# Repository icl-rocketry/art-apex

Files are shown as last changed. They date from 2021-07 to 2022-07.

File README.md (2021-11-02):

# art-apex
PCBs and software for ART's APEX rocket

# Contents

1. [Hardware](#Hardware)
2. [Software architecture](#SoftwareArchitecture)
3. [Next Steps](#NextSteps)

## Hardware

The flight computer for Apex consists of the following components:

1. [Tiny2040](https://shop.pimoroni.com/products/tiny-2040) microcontroller - for controlling each of the components
2. [BNO085](https://learn.adafruit.com/adafruit-9-dof-orientation-imu-fusion-breakout-bno085) 9DoF IMU - for recording and fusing flight data
3. [DPS310](https://www.infineon.com/cms/en/product/sensor/pressure-sensors/pressure-sensors-for-iot/dps310/) barometer - for recording altitude information
4. [Sim800L](https://nettigo.eu/products/sim800l-gsm-grps-module) GPRS/GSM module - for communication between the flight computer and ground team
5. [Adafruit mini GPS PA1010D](https://www.adafruit.com/product/4415) GPS module - for recovery
6. 3.7V 200maH LiPo battery - for powering the system
7. A 104 decibel speaker - for recovery

The Tiny2040 is connected to the BNO085, DPS310 and PA1010D via an I2C connection using GPIO pins 26 and 27. The Tiny2040 is connected to the Sim800L module via a UART connection using GPIO pins 4 and 5.

The SIM8000L **must** be isolated when the Tiny2040 is connected to USB, or else it will be fried.

## Software

The filesystem on board the Tiny2040 will look like this:
```
📦src
 ┣ 📂lib
 ┃ ┣ 📂adafruit_bno08x
 ┃ ┃ ┣ 📜debug.py
 ┃ ┃ ┣ 📜i2c.py
 ┃ ┃ ┗ 📜__init__.py
 ┃ ┣ 📂adafruit_bus_device
 ┃ ┃ ┣ 📜i2c_device.mpy
 ┃ ┃ ┣ 📜spi_device.mpy
 ┃ ┃ ┗ 📜__init__.py
 ┃ ┣ 📂adafruit_register
 ┃ ┃ ┣ 📜i2c_bcd_alarm.mpy
 ┃ ┃ ┣ 📜i2c_bcd_datetime.mpy
 ┃ ┃ ┣ 📜i2c_bit.mpy
 ┃ ┃ ┣ 📜i2c_bits.mpy
 ┃ ┃ ┣ 📜i2c_struct.mpy
 ┃ ┃ ┣ 📜i2c_struct_array.mpy
 ┃ ┃ ┗ 📜__init__.py
 ┃ ┣ 📜adafruit_dps310.mpy
 ┃ ┗ 📜adafruit_gps.py
 ┣ 📜boot.py
 ┣ 📜code.py
 ┣ 📜gps.py
 ┣ 📜led.py
 ┣ 📜phone.number
 ┣ 📜sensors.py
 ┣ 📜sms.py
 ┣ 📜speaker.py
 ┗ 📜state_machine.py
```

All folders inside the lib directory are libraries required for the Tiny2040 to interact with components. None of these files should be changed, except for lib/adafruit_bno08x/\_\_init__.py, where `_DEFAULT_REPORT_INTERVAL` should be set to 35ms. **Pro tip: don't lower this if you want to launch**.

`boot.py` runs right after the Tiny2040 boots up. Its sole purpose is to grant write permission to the Tiny2040. Due to the implementation of CircuitPython's filesystem either a laptop or the Tiny2040, can write to the Tiny2040's filesystem, so this ensures that the Tiny2040 has this permission.

`code.py` runs the main code of the AAS. It essentially runs through the state machine defined in `state_machine.py`.

`gps.py`, `led.py`, `sensors.py`, `speaker.py` and `sms.py` are [adapters](https://www.tutorialspoint.com/design_pattern/adapter_pattern.htm) around the peripherals discussed above. The adapter pattern is used to decouple the rest of the code from the specifics of these devices.

`state_machine.py` contains the bulk of the flight logic. It describes a (linear) [finite state machine](https://en.wikipedia.org/wiki/Finite-state_machine) with 5 states.

1. Diagnostic - initialises sensors and sends initial messages
2. Calibration - calibrates the BNO085 as described [here](https://www.ceva-dsp.com/wp-content/uploads/2019/10/BNO080_085-Datasheet.pdf) on page 39
3. Preflight - sleeps until the launch command is sent.
4. Flight - records 5 minutes of flight data, and sends data to the telemetry service.
5. Postflight - sends the rocket's location/plays the siren when asked. Also plays the siren once every 30 seconds.

The Flight stage is the most involved, so a brief explanation of its code can be found below.

```py
def run(self):
    i = 0
    led.colour(255, 0, 0)

    #Problem:
    #Sim module will need long (50ms+) waits to work
    #But we can't afford that in a single threaded environment
    #Solution:
    #Use pkt_wait to provide the sleeps
    pkt_wait = 1
    pkt = bytearray(sensors.data_size * 4)
    self._sms.connect()

    while i < self._flight_time:
        pkt_wait -= 1
        i += 1
        start = millis()
        data = self._sensors.get()
        for reading in data:
            self._sensor_storage.write(struct.pack("f", reading))

        if pkt_wait == 0:
            pkt[0:4] = struct.pack("f", data[0]) #time
            for j in range(4):
                pkt[4*j:4*(j+1)] = struct.pack("f", data[j+4])
            
            pkt[20:24] = struct.pack("f", data[10]) #altitude
            pkt_wait = self._sms.send_pkt(pkt)
        end = millis()
        sleep_ms(max(0, self._delay - (end - start)))

    self._sensor_storage.flush()
    self._sensor_storage.close()
    self._sms.disconnect()
    return postflight(self._sms, self._gps)
```

```py
led.colour(255, 0, 0)
```
First the Tiny2040's led is set to red to indicate flight.

```py
pkt_wait = 1
pkt = bytearray(sensors.data_size * 4)
self._sms.connect()
```
This code relates to the telemetry service. The Sim800L will connect to GPRS here (the internet) and send appropriate data via UDP. To save space, it will group several readings into a single packet.

```py
while i < self._flight_time:
    pkt_wait -= 1
    i += 1
    start = millis()
    data = self._sensors.get()
    for reading in data:
        self._sensor_storage.write(struct.pack("f", reading))

    if pkt_wait == 0:
        pkt[0:4] = struct.pack("f", data[0]) #time
        for j in range(4):
            pkt[4*j:4*(j+1)] = struct.pack("f", data[j+4])
        
        pkt[20:24] = struct.pack("f", data[10]) #altitude
        pkt_wait = self._sms.send_pkt(pkt)
    end = millis()
    sleep_ms(max(0, self._delay - (end - start)))
```

This is the main flight loop. It waits for `self._flight_time` readings to occur (assuming each reading takes at most `self._delay` ms).

```py
start = millis()
data = self._sensors.get()
for reading in data:
    self._sensor_storage.write(struct.pack("f", reading))
```
This code takes sensor readings, and records the time that they were taken, then writes them into a file. The values are stored as 32bit floating point numbers, to save space.
Note: the time recorded is milliseconds from the start.

```py
if pkt_wait == 0:
    pkt[0:4] = struct.pack("f", data[0]) #time
    for j in range(4):
        pkt[4*j:4*(j+1)] = struct.pack("f", data[j+4])
    
    pkt[20:24] = struct.pack("f", data[10]) #altitude
    pkt_wait = self._sms.send_pkt(pkt)
```
This adds the readings into the packet defined earlier, and if the packet is full it sends them.

The `pkt_wait` variable is used to solve a problem, which is that the Sim800l needs to wait around 200ms after it's sent a packet, before being able to send another one. However we can't perform this wait in the main loop, as that would lead to large delays in between recordings, so we define the `pkt_wait` variable to indicate whether we can send a packet. This allows us to use the main loop as a pseudo sleep (at the time of writing, the `uasynchio` library was not available).

```py
end = millis()
sleep_ms(max(0, self._delay - (end - start)))
```
This ensures that we always sleep for at least 50ms, regardless of how long different components take to work.

```py
self._sensor_storage.flush()
self._sensor_storage.close()
self._sms.disconnect()
return postflight(self._sms, self._gps)
```
Finally we flush the recordings, and close the file, then disconnect the Sim800L from GPRS and move on to the postflight stage. 

The end.

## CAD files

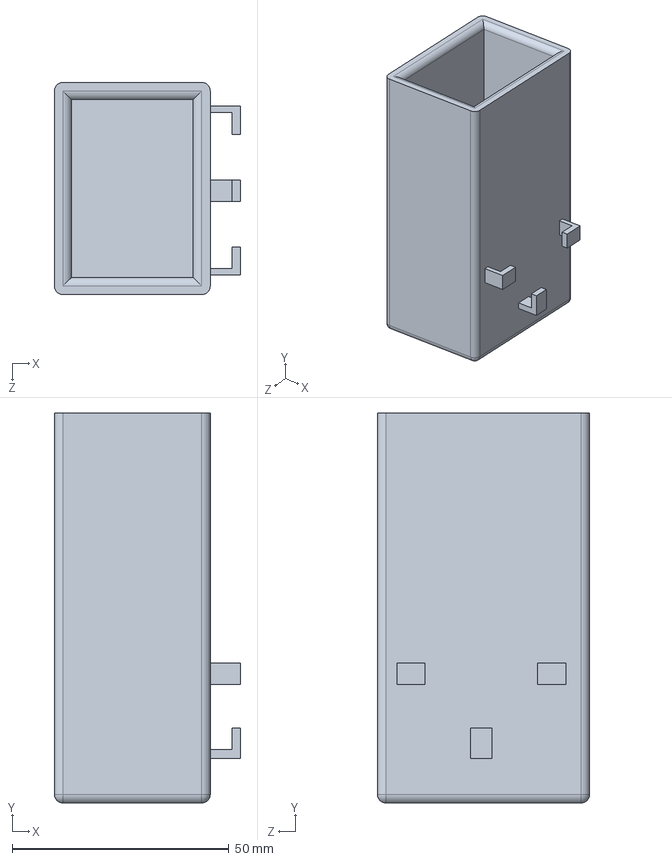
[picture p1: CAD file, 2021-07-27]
apex/test_bay/main.SLDPRT
43.0 x 90.0 x 49.0 mm

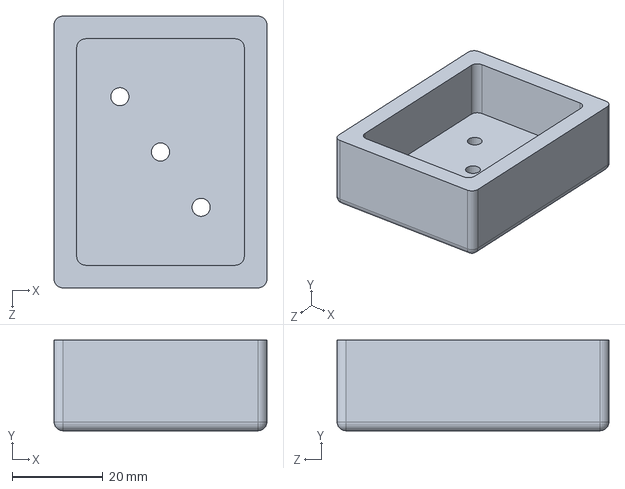
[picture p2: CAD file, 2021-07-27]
apex/test_bay/lid.SLDPRT
47.0 x 20.0 x 60.0 mm

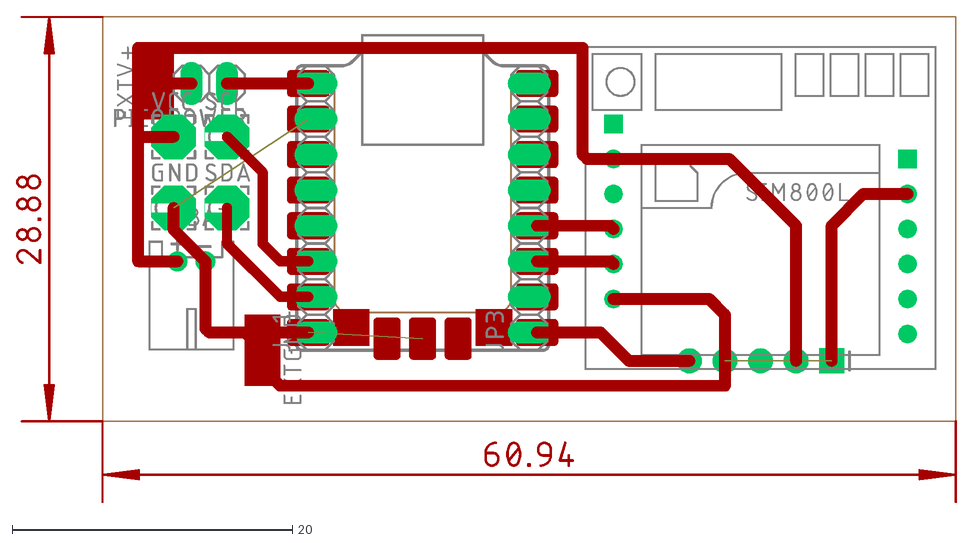
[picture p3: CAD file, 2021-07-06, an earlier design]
PCB/APEX/v2/lower_traced.dxf
67.2 x 34.8

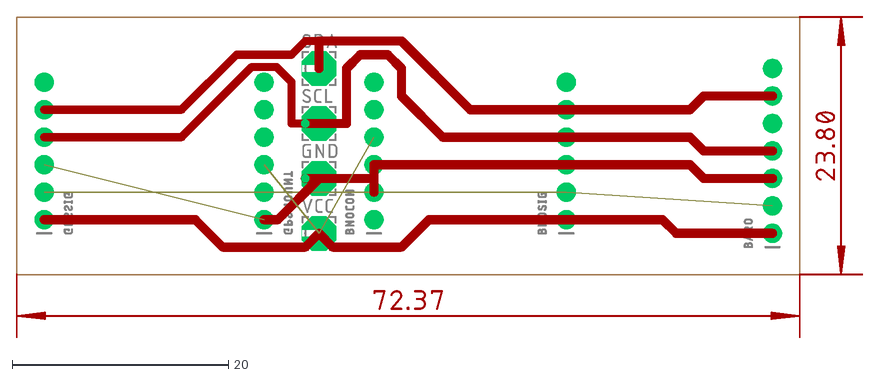
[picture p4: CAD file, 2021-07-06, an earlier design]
PCB/APEX/v2/upper_traced.dxf
78.3 x 29.7

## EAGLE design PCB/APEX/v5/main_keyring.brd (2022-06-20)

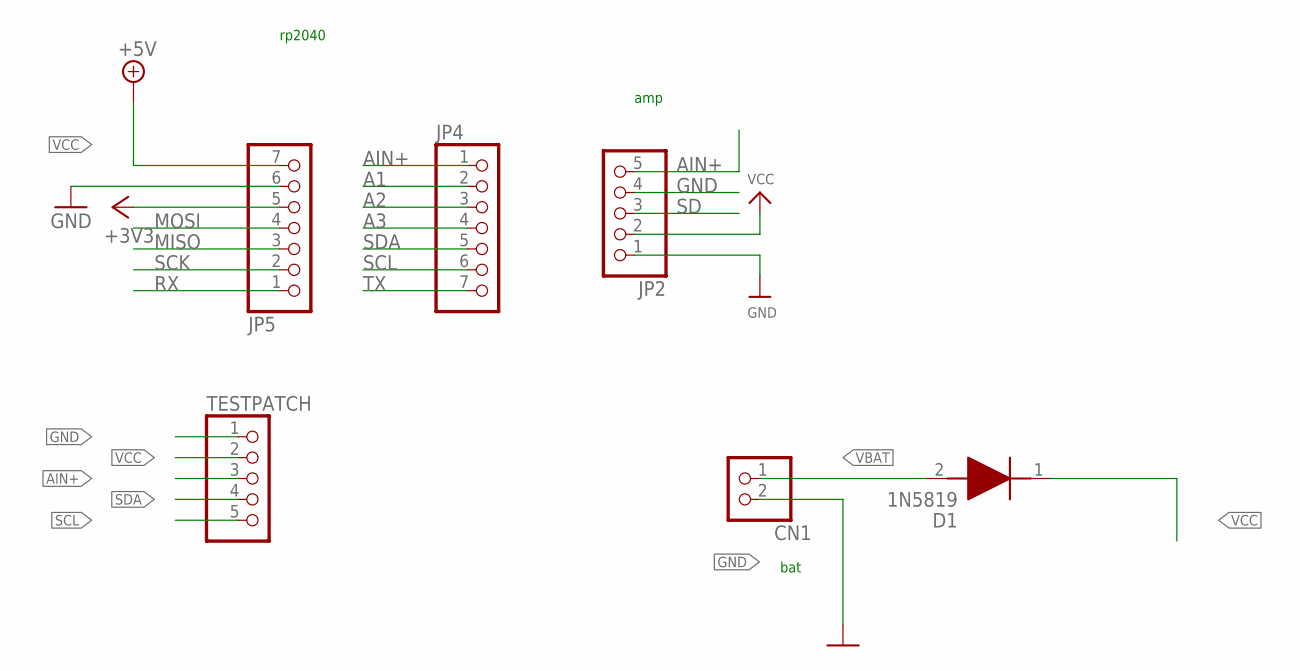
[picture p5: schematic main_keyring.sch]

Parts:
CN1: JST_2PIN-THM; JST-PH-2-THM
D1: 1N5819; DIOAD1414W86L464D238
JP2: HEADER-1X570MIL; 1X05_ROUND_70
JP4, JP5: HEADER-1X7; 1X07_OVAL
TESTPATCH: PINHD-1X5; 1X05

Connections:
+3V3: JP5.5
A1: JP4.2
A2: JP4.3
A3: JP4.4
AIN+: JP2.5, JP4.1, TESTPATCH.3
GND: CN1.2 (1), JP2.1, JP2.4, JP5.6, TESTPATCH.1
MISO: JP5.3
MOSI: JP5.4
RX: JP5.1
SCK: JP5.2
SCL: JP4.6, TESTPATCH.5
SD: JP2.3
SDA: JP4.5, TESTPATCH.4
TX: JP4.7
VBAT: CN1.1 (2), D1.2 (A)
VCC: D1.1 (K), JP2.2, JP5.7, TESTPATCH.2

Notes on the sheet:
amp
bat
rp2040

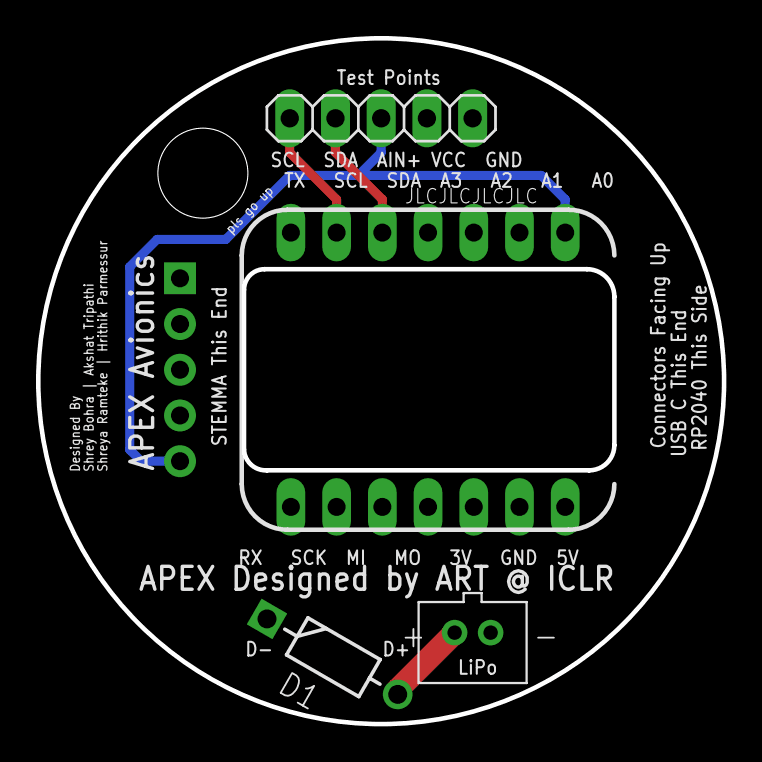
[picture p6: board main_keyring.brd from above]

Board: 2 copper layers, 38.1 x 38.1 mm, 6 parts (1 on the bottom side), 6 nets.

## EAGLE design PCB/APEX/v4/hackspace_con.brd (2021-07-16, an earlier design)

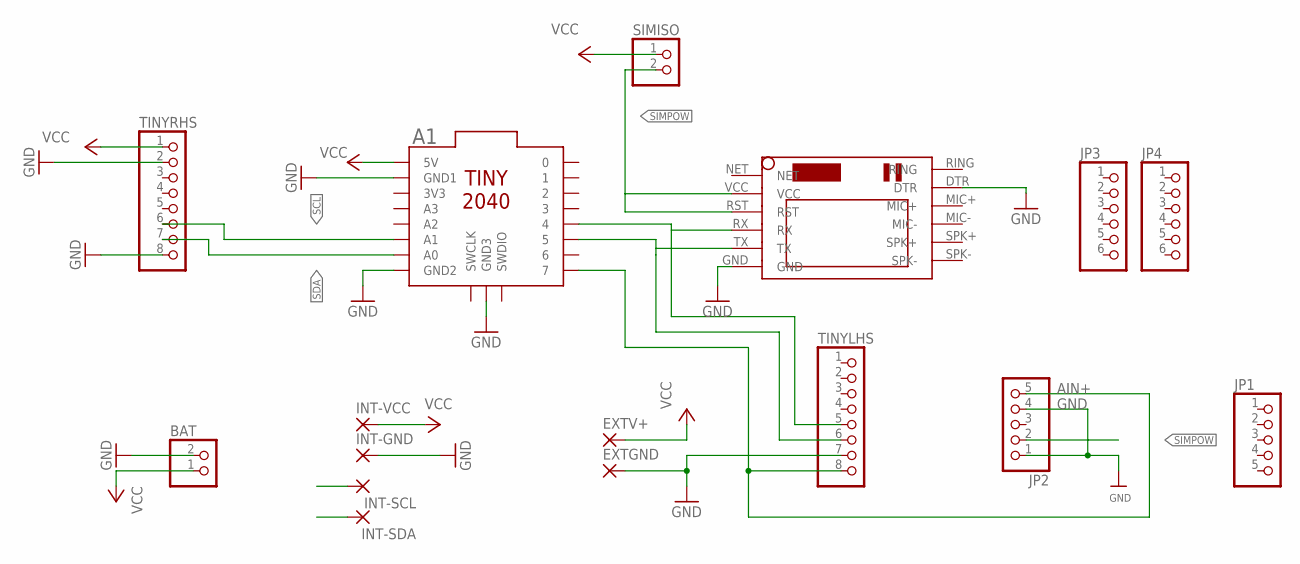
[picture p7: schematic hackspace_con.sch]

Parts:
A1: TINY2040
BAT: JST_2PIN-THM-RA; JST-PH-2-THM-RA
EXTGND: SMD5; SMD2,54-5,08
EXTV+: SMD5; SMD2,54-5,08
INT-GND: 3,17/1,1
INT-SCL: 3,17/1,1
INT-SDA: 3,17/1,1
INT-VCC: 3,17/1,1
JP1: PINHD-1X5; 1X05
JP2: HEADER-1X570MIL; 1X05_ROUND_70
JP3, JP4: PINHD-1X6; 1X06
SIMISO: PINHD-1X2; 1X02
TINYLHS: PINHD-1X8; 1X08
TINYRHS: PINHD-1X8; 1X08
U$1: SIM800LMODULE

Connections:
AIN+: A1.7, JP2.5, TINYLHS.8
GND: A1.GND1, A1.GND2, A1.GND3, BAT.2 (1), EXTGND.1, INT-GND.1, JP2.1, JP2.4, TINYLHS.7, TINYRHS.2, TINYRHS.8, U$1.DTR, U$1.GND
RX: A1.4, TINYLHS.5, U$1.RX
SCL: A1.A1, INT-SCL.1, TINYRHS.6
SDA: A1.A0, INT-SDA.1, TINYRHS.7
SIMPOW: JP2.2, SIMISO.2, U$1.RST, U$1.VCC
TX: A1.5, TINYLHS.6, U$1.TX
VCC: A1.5V, BAT.1 (2), EXTV+.1, INT-VCC.1, SIMISO.1, TINYRHS.1

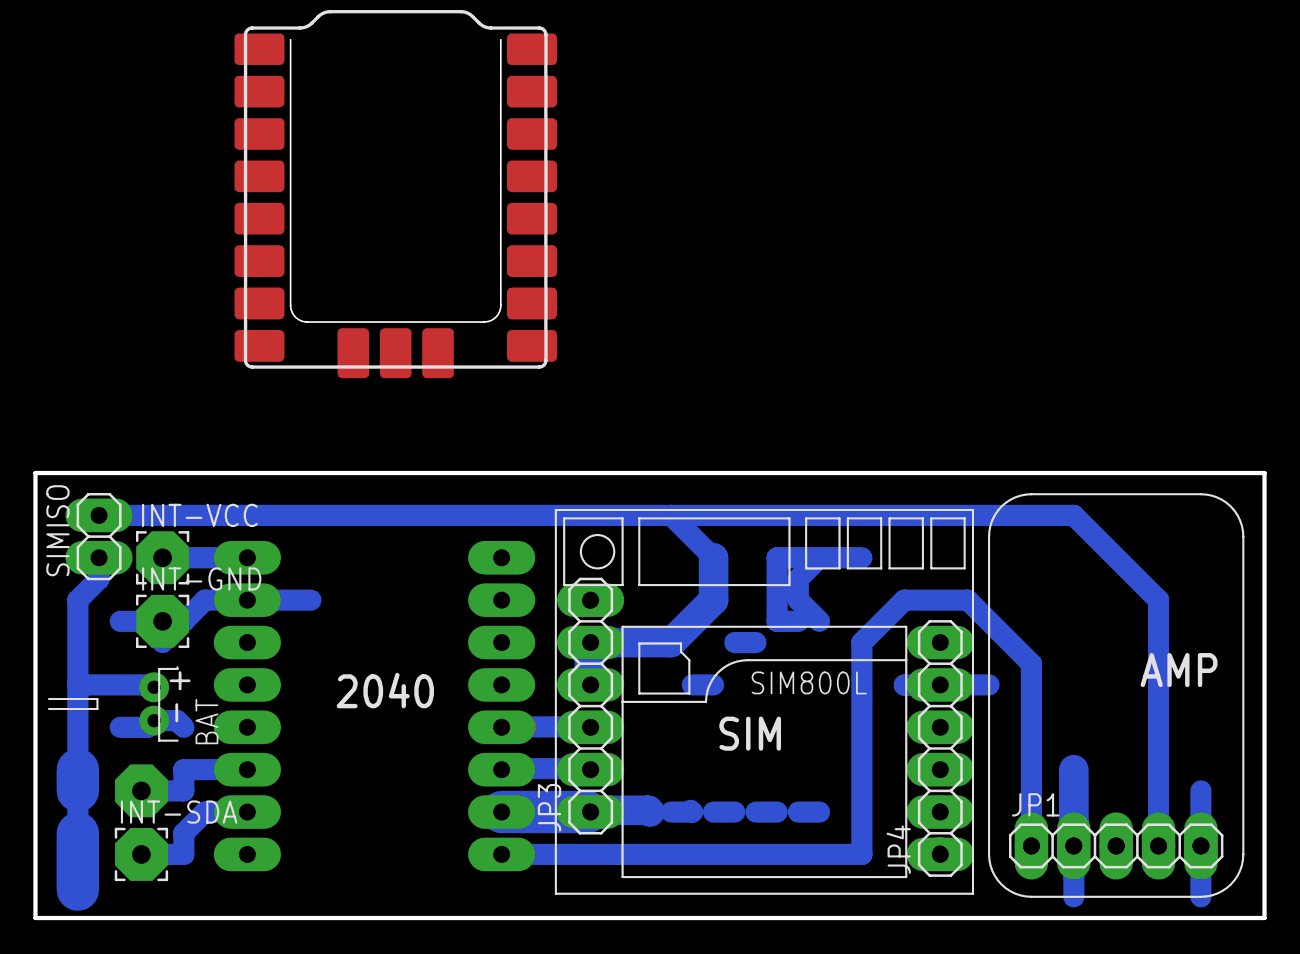
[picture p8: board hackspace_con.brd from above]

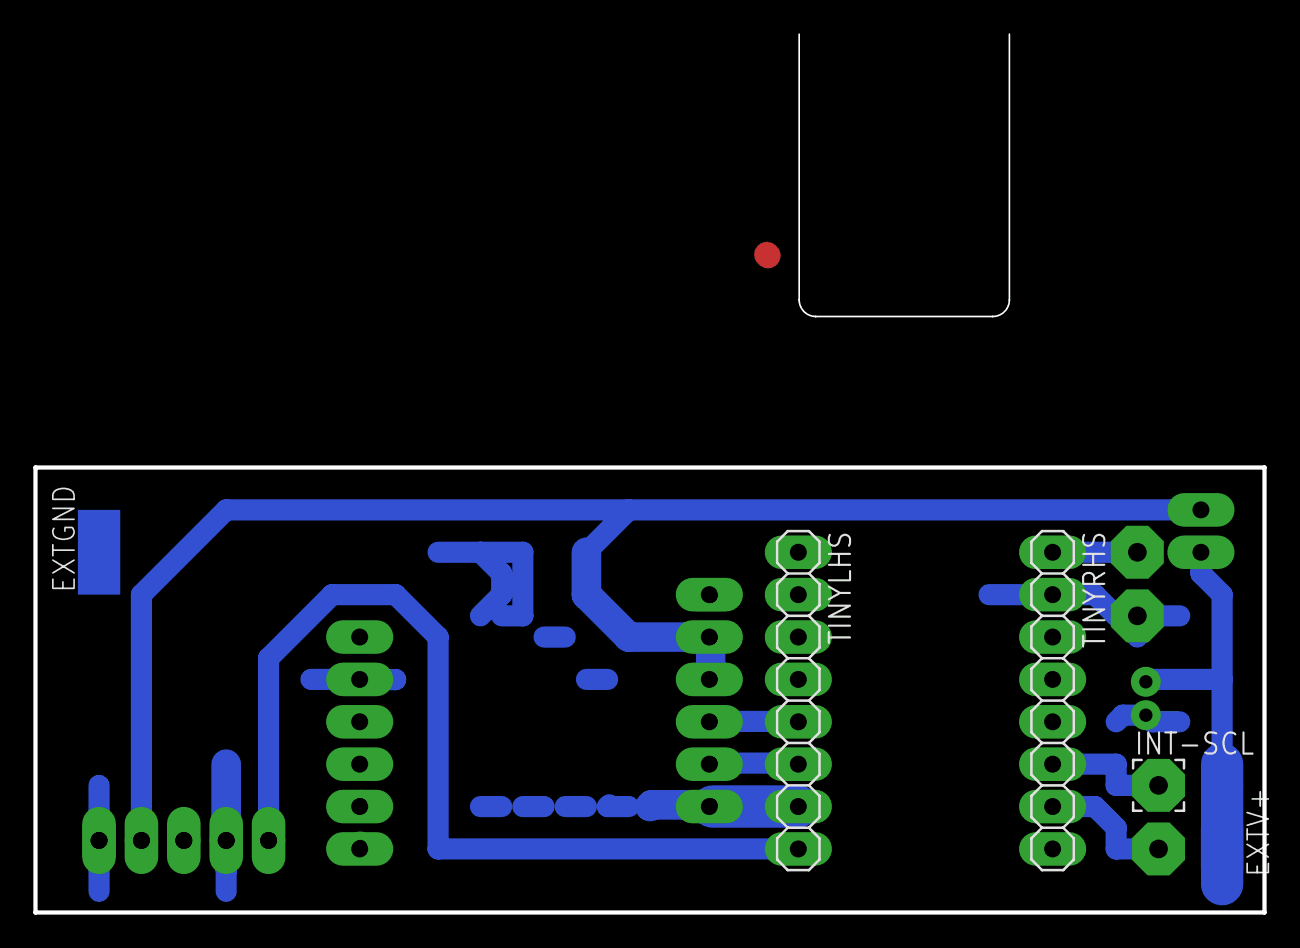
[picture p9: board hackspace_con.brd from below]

Board: 2 copper layers, 73.7 x 26.7 mm, 16 parts (5 on the bottom side), 8 nets.

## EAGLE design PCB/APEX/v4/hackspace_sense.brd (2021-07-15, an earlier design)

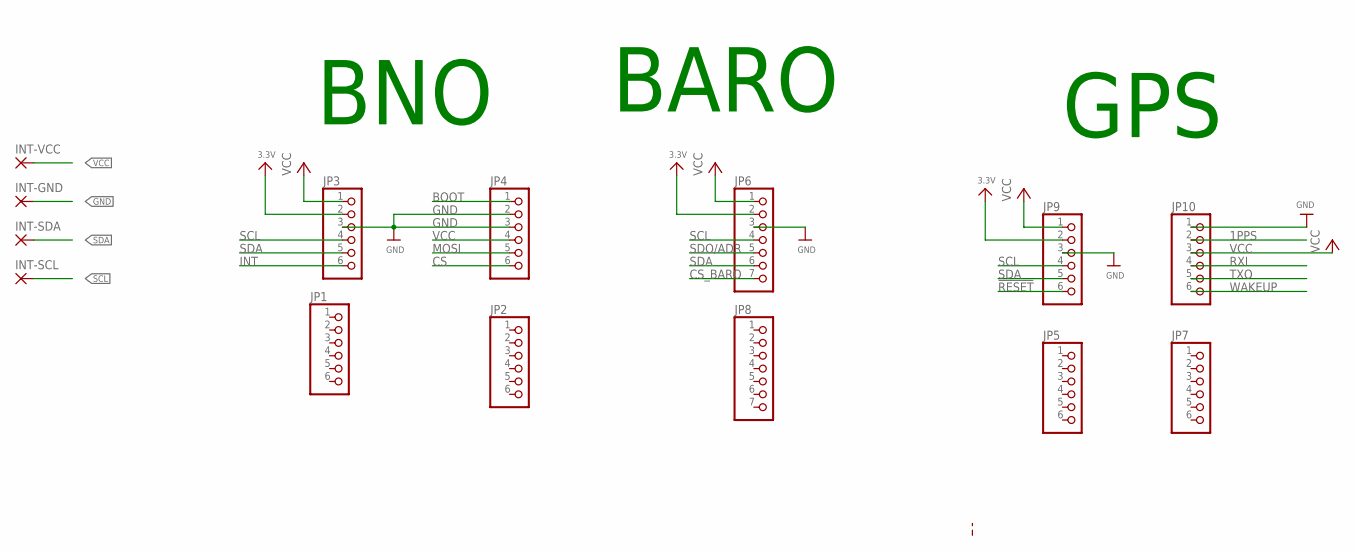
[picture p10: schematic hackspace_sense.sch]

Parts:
INT-GND: 3,17/1,1
INT-SCL: 3,17/1,1
INT-SDA: 3,17/1,1
INT-VCC: 3,17/1,1
JP1, JP2, JP5, JP7: PINHD-1X6; 1X06
JP3, JP4, JP9, JP10: HEADER-1X670MIL; 1X06_ROUND_70
JP6: HEADER-1X770MIL; 1X07_ROUND_70
JP8: PINHD-1X7; 1X07

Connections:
1PPS: JP10.2
3.3V_BARO: JP6.2
3.3V_BNO: JP3.2
3.3V_GPS: JP9.2
!RESET: JP9.6
BOOT: JP4.1
CS: JP4.6
CS_BARO: JP6.7
GND: INT-GND.1, JP3.3, JP4.2, JP4.3, JP6.3, JP9.3, JP10.1
INT: JP3.6
MOSI: JP4.5
RXI: JP10.4
SCL: INT-SCL.1, JP3.4, JP6.4, JP9.4
SDA: INT-SDA.1, JP3.5, JP6.6, JP9.5
SDO/ADR: JP6.5
TXO: JP10.5
VCC: INT-VCC.1, JP3.1, JP4.4, JP6.1, JP9.1, JP10.3
WAKEUP: JP10.6

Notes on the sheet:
BNO
BARO
GPS

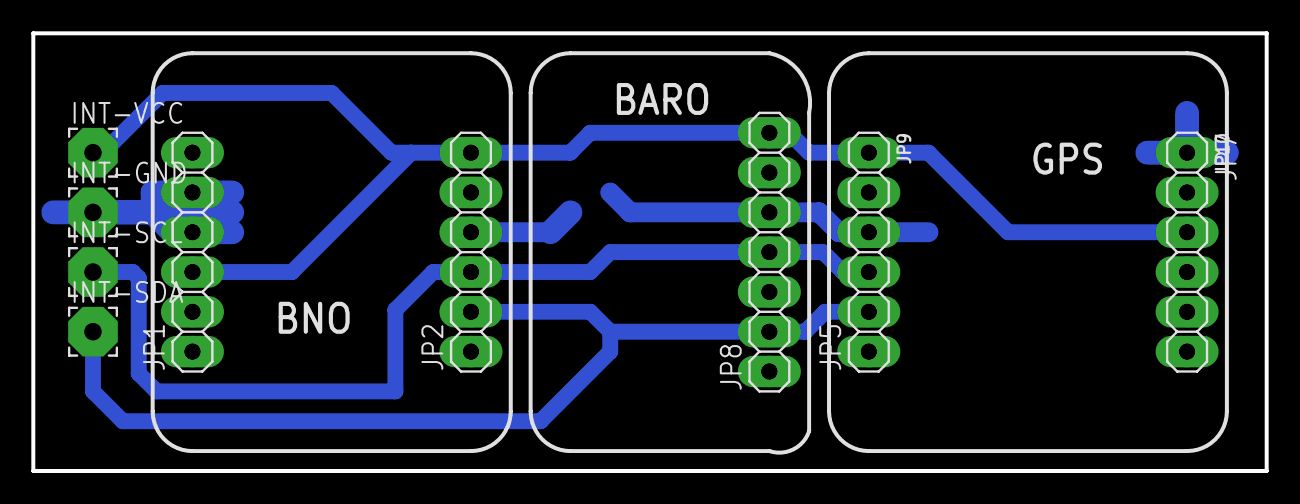
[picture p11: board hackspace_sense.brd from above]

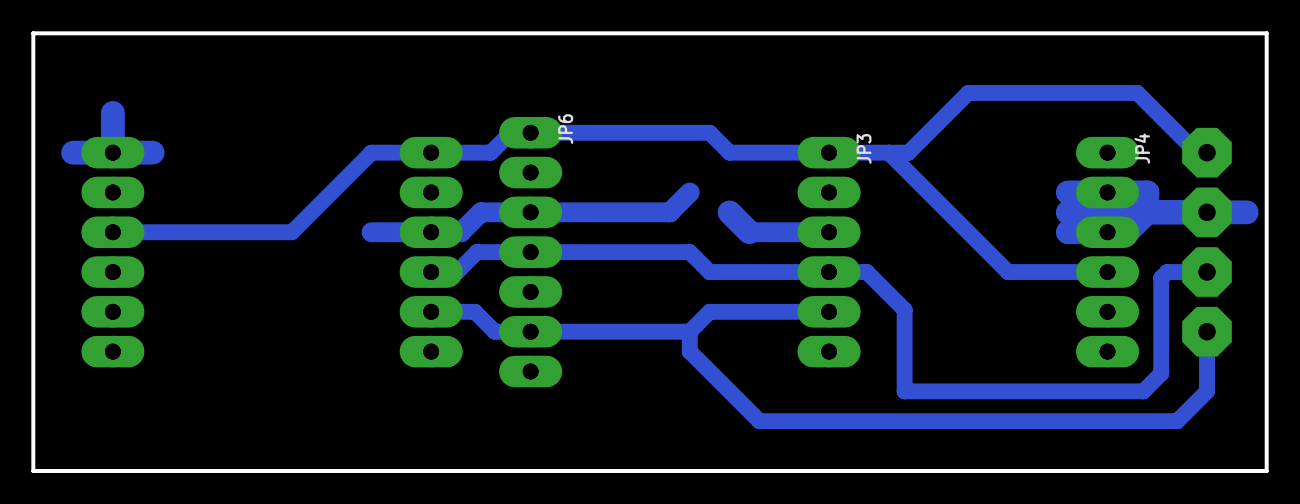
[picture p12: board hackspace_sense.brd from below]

Board: 2 copper layers, 78.7 x 27.9 mm, 14 parts (3 on the bottom side), 4 nets.

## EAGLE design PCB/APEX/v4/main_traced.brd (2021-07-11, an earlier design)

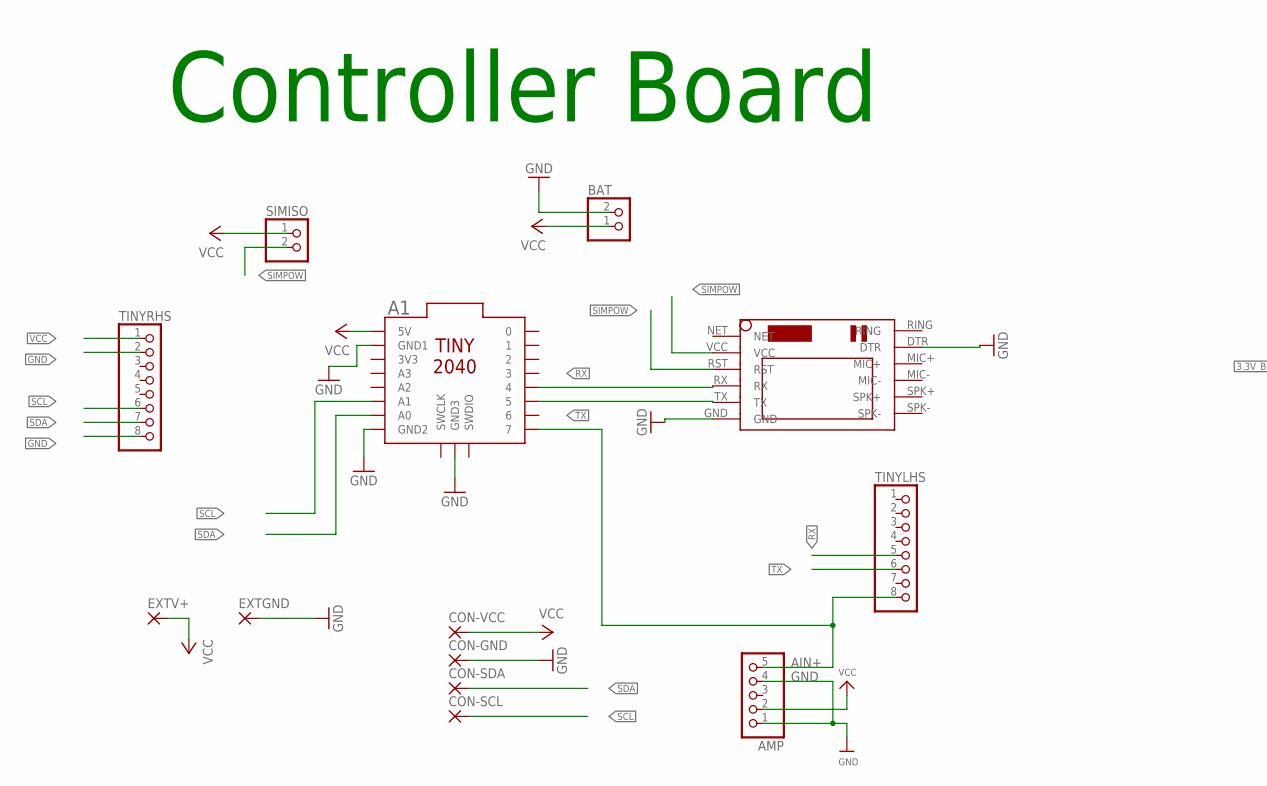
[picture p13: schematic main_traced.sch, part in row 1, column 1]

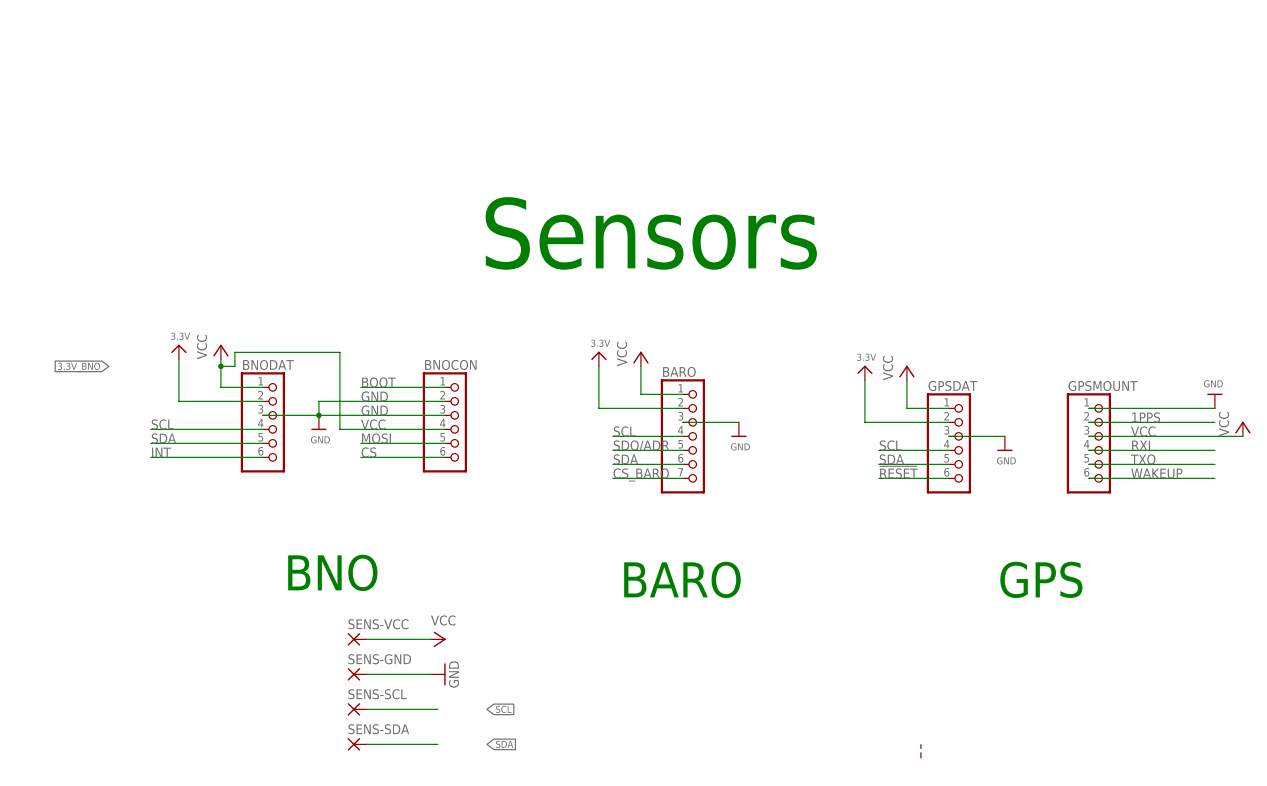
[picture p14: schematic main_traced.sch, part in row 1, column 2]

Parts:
A1: TINY2040
AMP: HEADER-1X570MIL; 1X05_ROUND_70
BARO: HEADER-1X770MIL; 1X07_ROUND_70
BAT: JST_2PIN-THM-RA; JST-PH-2-THM-RA
BNOCON: HEADER-1X670MIL; 1X06_ROUND_70
BNODAT: HEADER-1X670MIL; 1X06_ROUND_70
CON-GND: 3,17/1,3
CON-SCL: 3,17/1,3
CON-SDA: 3,17/1,3
CON-VCC: 3,17/1,3
EXTGND: SMD5; SMD2,54-5,08
EXTV+: SMD5; SMD2,54-5,08
GPSDAT: HEADER-1X670MIL; 1X06_ROUND_70
GPSMOUNT: HEADER-1X670MIL; 1X06_ROUND_70
SENS-GND: 3,17/1,3
SENS-SCL: 3,17/1,3
SENS-SDA: 3,17/1,3
SENS-VCC: 3,17/1,3
SIMISO: PINHD-1X2; 1X02
TINYLHS: PINHD-1X8; 1X08
TINYRHS: PINHD-1X8; 1X08
U$1: SIM800LMODULE

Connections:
1PPS: GPSMOUNT.2
3.3V_2: BARO.2
3.3V_3: GPSDAT.2
3.3V_BNO: BNODAT.2
!RESET: GPSDAT.6
AIN+: A1.7, AMP.5, TINYLHS.8
BOOT: BNOCON.1
CS: BNOCON.6
CS_BARO: BARO.7
GND: A1.GND1, A1.GND2, A1.GND3, AMP.1, AMP.4, BARO.3, BAT.2 (1), BNOCON.2, BNOCON.3, BNODAT.3, CON-GND.1, EXTGND.1, GPSDAT.3, GPSMOUNT.1, SENS-GND.1, TINYRHS.2, TINYRHS.8, U$1.DTR, U$1.GND
INT: BNODAT.6
MOSI: BNOCON.5
RX: A1.4, TINYLHS.5, U$1.RX
RXI: GPSMOUNT.4
SCL: A1.A1, BARO.4, BNODAT.4, CON-SCL.1, GPSDAT.4, SENS-SCL.1, TINYRHS.6
SDA: A1.A0, BARO.6, BNODAT.5, CON-SDA.1, GPSDAT.5, SENS-SDA.1, TINYRHS.7
SDO/ADR: BARO.5
SIMPOW: SIMISO.2, U$1.RST, U$1.VCC
TX: A1.5, TINYLHS.6, U$1.TX
TXO: GPSMOUNT.5
VCC: A1.5V, AMP.2, BARO.1, BAT.1 (2), BNOCON.4, BNODAT.1, CON-VCC.1, EXTV+.1, GPSDAT.1, GPSMOUNT.3, SENS-VCC.1, SIMISO.1, TINYRHS.1
WAKEUP: GPSMOUNT.6

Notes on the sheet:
Controller Board
BNO
BARO
GPS
Sensors

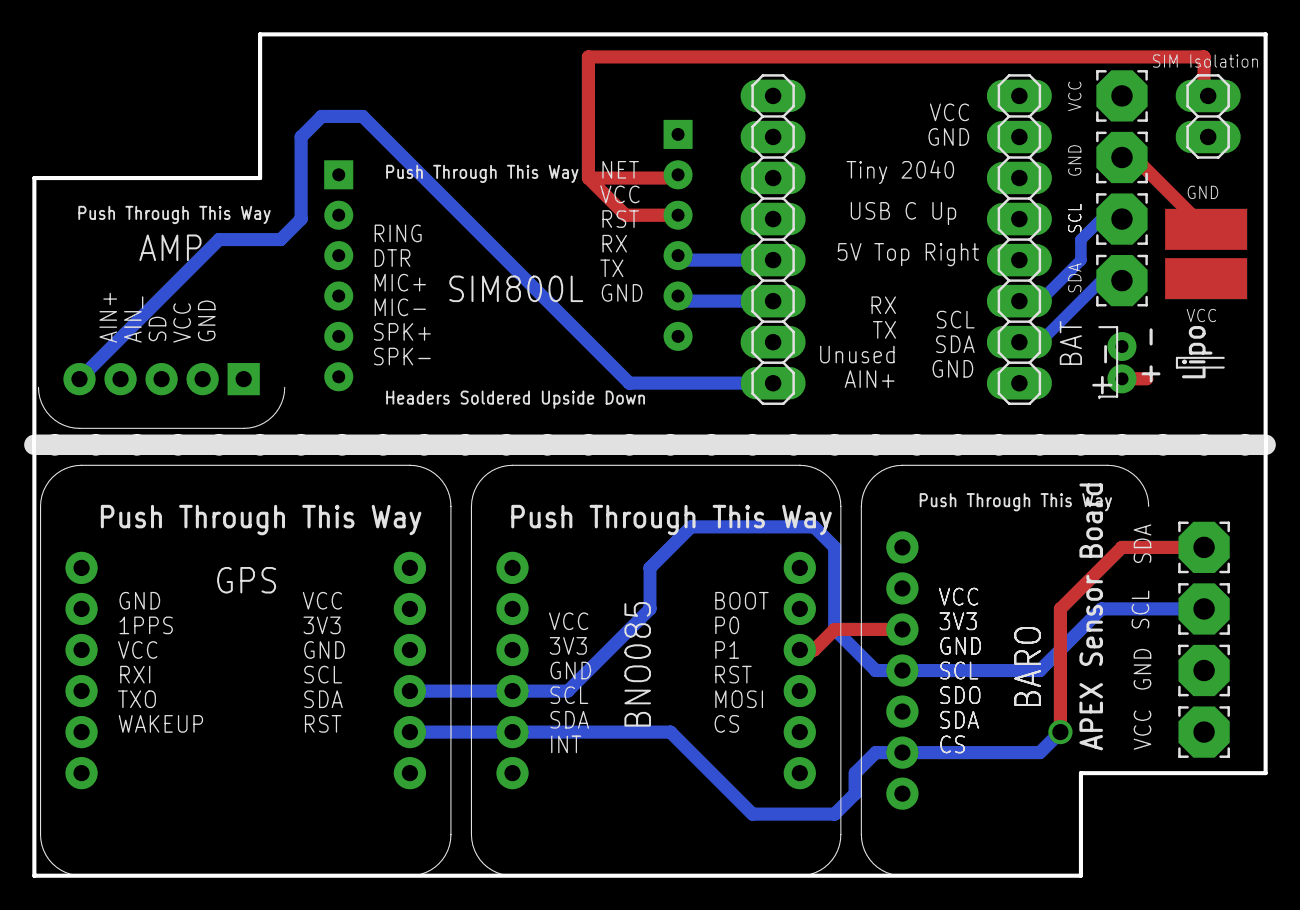
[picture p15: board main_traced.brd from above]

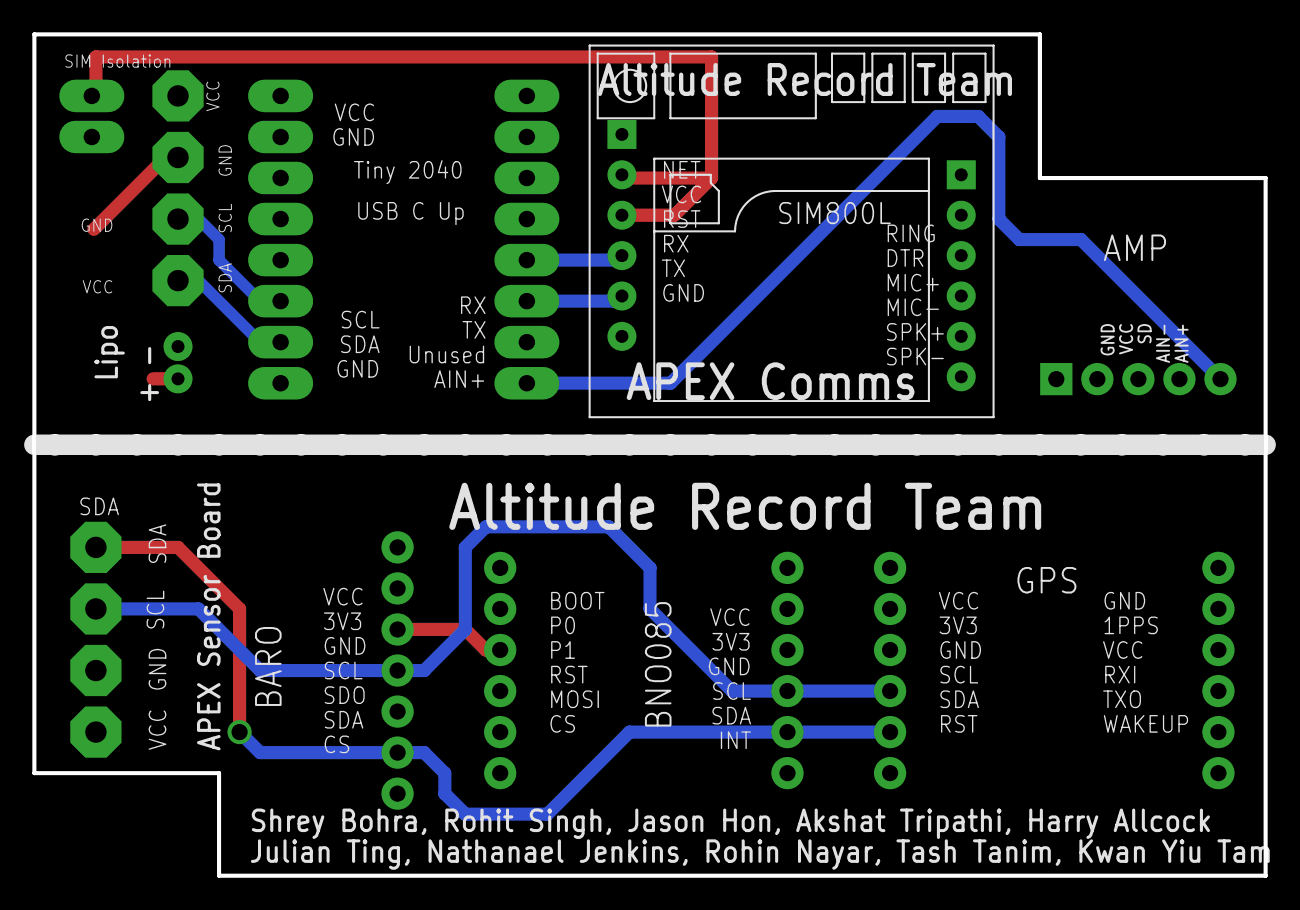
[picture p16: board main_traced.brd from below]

Board: 2 copper layers, 76.2 x 52.1 mm, 21 parts (3 on the bottom side), 8 nets.

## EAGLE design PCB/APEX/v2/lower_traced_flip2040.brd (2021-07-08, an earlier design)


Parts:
A1: TINY2040
BAT: JST_2PIN-THM-RA; JST-PH-2-THM-RA
GND: 3,17/1,1
JP2: HEADER-1X570MIL; 1X05_ROUND_70
PICOPOWER: PINHD-1X2; 1X02
SCL: 3,17/1,1
SDA: 3,17/1,1
TINYLHS: PINHD-1X8; 1X08
TINYRHS: PINHD-1X8; 1X08
U$2: SIM800LMODULE
VCC: 3,17/1,1

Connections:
AIN+: A1.7, JP2.5, TINYLHS.8
GND: A1.GND1, A1.GND2, A1.GND3, BAT.2 (1), GND.1, JP2.1, JP2.4, TINYRHS.2, TINYRHS.8, U$2.DTR, U$2.GND
unnamed: A1.4, TINYLHS.5, U$2.RX
unnamed: A1.5, TINYLHS.6, U$2.TX
unnamed: A1.A1, SCL.1, TINYRHS.6
unnamed: A1.A0, SDA.1, TINYRHS.7
unnamed: A1.5V, PICOPOWER.1, TINYRHS.1
unnamed: A1.6, TINYLHS.7
unnamed: A1.3, TINYLHS.4
unnamed: A1.2, TINYLHS.3
unnamed: A1.1, TINYLHS.2
unnamed: A1.0, TINYLHS.1
unnamed: A1.A2, TINYRHS.5
unnamed: A1.A3, TINYRHS.4
unnamed: A1.3V3, TINYRHS.3
VCC: BAT.1 (2), JP2.2, PICOPOWER.2, U$2.VCC, VCC.1



Board: 2 copper layers, 60.9 x 28.9 mm, 11 parts (3 on the bottom side), 16 nets.

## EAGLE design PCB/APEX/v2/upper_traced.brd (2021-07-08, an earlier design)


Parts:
BARO: HEADER-1X770MIL; 1X07_ROUND_70
BNOCON: HEADER-1X670MIL; 1X06_ROUND_70
BNOSIG: HEADER-1X670MIL; 1X06_ROUND_70
GND: 3,17/1,1
GPSMOUNT: HEADER-1X670MIL; 1X06_ROUND_70
GPSSIG: HEADER-1X670MIL; 1X06_ROUND_70
SCL: 3,17/1,1
SDA: 3,17/1,1
VCC: 3,17/1,1

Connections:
+3V3: BARO.2, BNOSIG.2, GPSSIG.2
GND: BARO.3, BNOCON.2, BNOCON.3, BNOSIG.3, GND.1, GPSMOUNT.1, GPSSIG.3
SCL: BARO.4, BNOSIG.4, GPSSIG.4, SCL.1
SDA: BARO.6, BNOSIG.5, GPSSIG.5, SDA.1
VCC: BARO.1, BNOCON.4, BNOSIG.1, GPSMOUNT.3, GPSSIG.1, VCC.1

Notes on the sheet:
bno
dps
gps



Board: 2 copper layers, 72.4 x 23.8 mm, 9 parts (2 on the bottom side), 5 nets.

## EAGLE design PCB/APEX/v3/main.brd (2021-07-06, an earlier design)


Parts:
AMP: HEADER-1X570MIL; 1X05_ROUND_70
BARO: HEADER-1X770MIL; 1X07_ROUND_70
BNOCON: HEADER-1X670MIL; 1X06_ROUND_70
BNOSIG: HEADER-1X670MIL; 1X06_ROUND_70
CN1: JST_2PIN-THM-RA; JST-PH-2-THM-RA
EXTGND: SMD5; SMD2,54-5,08
EXTV+: SMD5; SMD2,54-5,08
GPSMOUNT: HEADER-1X670MIL; 1X06_ROUND_70
GPSSIG: HEADER-1X670MIL; 1X06_ROUND_70
RP2040: TINY2040
RPSWITCH: PINHD-1X2; 1X02
U$1: SIM800LMODULE

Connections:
3.3V: BARO.2, BNOSIG.2, GPSSIG.2
AIN+: AMP.5, RP2040.7
GND: AMP.1, AMP.4, BARO.3, BNOCON.2, BNOCON.3, BNOSIG.3, CN1.2 (1), EXTGND.1, GPSSIG.3, RP2040.GND1, RP2040.GND2, RP2040.GND3, U$1.DTR, U$1.GND
unnamed: RP2040.4, U$1.RX
unnamed: RP2040.5, U$1.TX
unnamed: RP2040.5V, RPSWITCH.1
SCL: BARO.4, BNOSIG.4, GPSSIG.4, RP2040.A1
SDA: BARO.6, BNOSIG.5, GPSSIG.5, RP2040.A0
VCC: AMP.2, BARO.1, BNOCON.4, BNOSIG.1, CN1.1 (2), EXTV+.1, GPSSIG.1, RPSWITCH.2, U$1.VCC

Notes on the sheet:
bno
dps
gps
amp


Board: 2 copper layers, 160.0 x 100.0 mm, 12 parts (0 on the bottom side), 9 nets.

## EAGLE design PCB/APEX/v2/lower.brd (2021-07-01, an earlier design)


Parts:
A1: TINY2040
BAT: JST_2PIN-THM-RA; JST-PH-2-THM-RA
INTERCONNECT: PINHD-1X4; 1X04
JP1, JP3: PINHD-1X8; 1X08
JP2: HEADER-1X570MIL; 1X05_ROUND_70
U$2: SIM800LMODULE

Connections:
AIN+: A1.7, JP2.5
GND: A1.GND1, A1.GND2, A1.GND3, BAT.2 (1), INTERCONNECT.2, JP2.1, JP2.4, U$2.DTR, U$2.GND
unnamed: A1.4, U$2.RX
unnamed: A1.5, U$2.TX
unnamed: A1.A1, INTERCONNECT.3
unnamed: A1.A0, INTERCONNECT.4
VCC: A1.5V, BAT.1 (2), INTERCONNECT.1, JP2.2, U$2.VCC

Board: 2 copper layers, 7 parts (0 on the bottom side), 7 nets, no tracks yet.

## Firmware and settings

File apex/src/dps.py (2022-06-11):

from adafruit_dps310.advanced import DPS310, SampleCount, Rate, Mode
import busio
from board import *
import time

i2c = busio.I2C(SCL1, SDA1)

dps310 = DPS310(i2c)
dps310.pressure_oversample_count = SampleCount.COUNT_2
dps310.pressure_rate = Rate.RATE_16_HZ
dps310.temperature_oversample_count = SampleCount.COUNT_16
dps310.temperature_rate = Rate.RATE_16_HZ
dps310.mode = Mode.CONT_PRESTEMP

while True: 
    print("Temperature = %.2f *C"%dps310.temperature)
    print("Pressure = %.2f hPa"%dps310.pressure)
    print("")
    time.sleep(0.01)

i2c.deinit()

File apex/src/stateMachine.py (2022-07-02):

from time import sleep, monotonic_ns
from sensors import Sensors
from speaker import Speaker
import neopixel
import board
import os

# barometer ; BNO - acc, gyro, magno ; speaker 

DATA_RATE = 10  # 10 Hz
TIME_INTERVAL_DATA_TRANSFER = 1 / DATA_RATE
RECORDING_TIME = 15 * 60 #15 * 60
N_RECORDINGS = RECORDING_TIME * DATA_RATE
PREFLIGHT_WAIT_TIME = 30 * 60 # 30 * 60

pixel = neopixel.NeoPixel(board.NEOPIXEL, 1) #type: ignore
pixel.brightness = 0.3

class state:
    colour = (0, 0, 0)
    def __init__(self, speaker : Speaker, sensors : Sensors):
        self.speaker = speaker
        self.sensors = sensors

    def _run(self) -> type[state] | None:
        raise NotImplementedError()

    def run (self) -> type[state] | None:
        pixel.fill(self.colour)
        try:
            next_state = self._run()
        except Exception as e:
            pixel.fill((255, 0, 0))
            self.speaker.longBeep(3)
            raise e
       
        self.speaker.beep(self.stateid)
        if next_state != None:
            return next_state(self.speaker, self.sensors)


class diagnostic(state):
    stateid = 1
    colour = (255, 255, 0) ## yellow

    def __init__(self):
        pass

    def _run (self) -> type[calA]:
        print("Diagnostic state")
        self.speaker = Speaker()
        self.sensors = Sensors()
        if "datafile" in os.listdir():
            raise Exception("Datafile currently exists, can't record")
        elif "boot.py" not in os.listdir():
            raise Exception("Can't write data - no boot.py found")
        return calA

class calA(state):
    stateid = 2
    colour = (0, 0, 255) ##Blue

    def _run (self) -> type[calG]:
        self.sensors.calibrate()
        sleep(2)
        print("Calibration Acc state")
        return calG

class calG(state):
    stateid = 3
    colour = (255, 255, 255) #white

    def _run (self) -> type[calM]:
        print("Calibration Gyro state")
        sleep(2)
        return calM

class calM(state):
    stateid = 4
    colour = (255, 0, 255) #magenta 

    def _run (self) -> type[calStatic]:
        print("Calibration Magnetometer state")
        sleep(2)
        return calStatic


class calStatic(state):
    stateid = 5
    colour = (0, 255, 255) #cyan

    def _run (self) -> type[preFlight]:
        print("Static Calibration state")
        sleep(5)
        return preFlight


class preFlight(state):
    stateid = 6
    colour = (255,165,0) #orange 

    def _run (self) -> type[flight]:
        print("Pre flight state")
        sleep(PREFLIGHT_WAIT_TIME)
        self.speaker.playsong("rick.mp3")
        return flight


class flight(state):
    stateid = 7
    colour = (255, 0, 0) #red
    def _run (self) -> type[postFlight]:
        print("Flight state")
        try:
            f = open("datafile", "wb")
            for _ in range(N_RECORDINGS):
                start_time = monotonic_ns()
                data = self.sensors.packData()
                f.write(data)
                end_time = monotonic_ns()
                time_taken = (end_time - start_time) / 1000_000_000
                sleep(max(0, TIME_INTERVAL_DATA_TRANSFER - time_taken))
        except Exception as e:
            print(e)
        finally:
            f.flush()
            f.close()
        return postFlight

class postFlight(state):
    stateid = 8
    colour = (108, 122, 137) #greyish blue      
    def _run(self) -> None:
        print("Post flight state")
        self.speaker.siren(3)
        self.speaker.noise()
        self.speaker.shutup()
        sleep(60*20)
        while True:
            self.speaker.siren(1)
            self.speaker.noise()
            self.speaker.shutup()
            sleep(60)

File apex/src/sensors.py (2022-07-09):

from time import monotonic_ns
import struct
from adafruit_dps310.advanced import DPS310, Mode, Rate, SampleCount
import board
from busio import I2C


#Data structure:
# Time: uint32
# Pressure: float32
# Temperature: float32

_DATA_SIZE = 3 * 4

class Sensors:
    _bytes = bytearray(_DATA_SIZE)

    def __init__(self) -> None:
        i2c = I2C(sda=board.SDA1, scl=board.SCL1) #type: ignore
        self._dps = DPS310(i2c)
        self._dps.reset()
        self._dps.pressure_oversample_count = SampleCount.COUNT_4 #type: ignore
        self._dps.pressure_rate = Rate.RATE_64_HZ #type: ignore
        self._dps.temperature_oversample_count = SampleCount.COUNT_4 #type: ignore
        self._dps.temperature_rate = Rate.RATE_64_HZ #type: ignore
        self._dps.mode = Mode.CONT_PRESTEMP #type: ignore
      
        self._dps.initialize()
        self._dps.wait_pressure_ready()
        self._dps.wait_temperature_ready()


    def packData(self) -> bytearray:
        now = monotonic_ns() // 1_000_000 #To ms
        pressure = self._dps.pressure
        temperature = self._dps.temperature

        struct.pack_into("I", self._bytes, 0, now)
        struct.pack_into("f", self._bytes, 4, pressure)
        struct.pack_into("f", self._bytes, 8, temperature)

        return self._bytes

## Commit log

2021-07-01 get apex boards
2021-07-01 complete apex avionics schematic
    [main.brd, main.sch]
2021-07-01 switch to stacked approach
    [upper.brd, upper.sch]
2021-07-01 create boards
    [lower.brd, lower.sch, lower_traced.brd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]
2021-07-01 dimension boards
    [lower_traced.brd, upper_traced.brd]
2021-07-06 Switched to circuitpython
2021-07-06 Added sensors skeleton
2021-07-06 realign sim
    [lower_traced.dxf, main.brd, main.sch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]
2021-07-07 embiggen pads
    [lower_traced.brd, upper_traced.brd]
2021-07-07 tie bno reset high
    [upper_traced.brd]
2021-07-07 reroute gps vcc
    [upper_traced.brd]
2021-07-07 add labels upper
    [upper_traced.brd]
2021-07-08 add labels, embiggen pads
    [upper_traced.brd]
2021-07-08 flip tiny
    [lower_traced_flip2040.brd, lower_traced_flip2040.sch]
2021-07-09 test pcb
2021-07-09 Added sensors
2021-07-09 gps now takes an i2c object as a dependency injection
2021-07-10 increase i2c freq, timeout
2021-07-10 production board
    [main.brd, main.sch]
2021-07-10 add sensors
2021-07-10 complete layout
    [main.brd]
2021-07-10 use drc to increase pad size
    [main.brd, main.sch]
2021-07-10 replace tiny footprint with headers
    [main_traced.brd, main_traced.sch]
2021-07-11 add mill slots
    [main_traced.brd]
2021-07-11 undo milling, fix labels
    [main_traced.brd]
2021-07-11 transfer changes to parent file
    [main.brd, main.sch, main_traced.brd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]
2021-07-11 ground pour
    [main_traced.brd]
2021-07-11 add labels
    [main_traced.brd]
2021-07-11 fix label alignment
    [main_traced.brd]
2021-07-11 send changes to parent design
    [main.brd]
2021-07-11 implement vcc plane
    [main_traced.brd, main_traced.sch]
2021-07-11 battery connector cutout
    [main_traced.brd]
2021-07-11 final annotations
    [main_traced.brd]
2021-07-11 backport changes to parent design
    [main.brd, main.sch]
2021-07-11 remove tiny 2040 footprint
    [main_traced.brd]
2021-07-12 v5 boards for manufacturing at hackspace
    [hackspace_con.brd, hackspace_con.sch, hackspace_sense.brd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]
2021-07-12 increase trace widths
    [hackspace_sense.brd]
2021-07-14 control onboard led
2021-07-14 create class to control onboard led
2021-07-14 flip installation orientation
    [hackspace_con.brd]
2021-07-14 remove 2040 footprint
    [hackspace_con.brd]
2021-07-14 thiccer traces
    [hackspace_con.brd]
2021-07-14 flip amp
    [hackspace_con.brd]
2021-07-14 revert flip amp
    [hackspace_con.brd]
2021-07-14 fix git revert issues
    [hackspace_con.brd]
2021-07-14 ground pin 7
    [hackspace_con.brd, hackspace_con.sch]
2021-07-16 mirror pdf
    [hackspace_con.brd]
2021-07-18 utilise led class
2021-07-19 Added diagnostic stage and inverted dependencies
2021-07-27 Added avionics test bay design
    [lid.SLDPRT, main.SLDPRT]
2021-08-05 Added voltage check results
2021-08-05 Added threejs visualisation of apex
    [apex.STL]
2021-08-17 Minor changes
    [voltage1.csv]
2021-08-19 Switched to asyncio - day ruined
2021-08-19 Added example data
    [sample_data.csv]
2021-08-19 Fixed sample data units - m/s^2 to g, and degrees to radians
    [sample_data.csv]
2021-08-25 Refactored sensors to allow individual sensors to fail without affecting others + added raw accelerometer values
    [sensors.py]
2021-08-25 Sensors now reports raw gyroscope and magnetometer values
2021-08-27 Fixed stuff
    [sample_data.csv]
2021-08-27 Added calibration stage
2021-08-28 Sms recv_msg now causes the led to blink
2021-10-31 modify data collection
    [data.csv]
2021-10-31 battery testing data
    [sim_only.csv]
2021-10-31 telemetry development was moved to its own repo
    [apex.STL, sample_data.csv]
2021-11-01 sim800l voltage requirements
2021-11-30 Made v5 of apex board
    [main.brd, main.sch]
2021-11-30 completed pcb
    [main.brd]
2021-12-09 remove double frame
    [main.sch]
2021-12-09 flip battery connector
    [main.brd]
2021-12-09 mill slot under rp2040 chip
    [main.brd]
2021-12-09 move boards inside slightly
    [main.brd]
2021-12-09 reroute trace around slot
    [main.brd]
2021-12-09 introduce test points, rotate mcu for better usb pos
    [main.brd, main.sch]
2021-12-09 reroute traces post flip
    [main.brd]
2021-12-09 increase clearance for stemma port
    [main.brd]
2021-12-10 add helpful labels
    [main.brd]
2021-12-10 swap testpoints for easier routing
    [main.brd, main.sch]
2021-12-12 change footprint to remove castellations
2021-12-12 update rp2040 from new design block
    [main.brd, main.sch]
2021-12-12 enlarge pads to replace castellation
    [main.brd]
2021-12-12 mill clearance under rp2040
    [main.brd]
2021-12-12 scale to 7.4mm
2021-12-12 move mill to dimension layer
    [main.brd]
2021-12-12 flipped logo
    [main.brd]
2021-12-12 apply aisler drc
    [main.brd]
2021-12-12 add m3 mounting hole
    [main.brd]
2021-12-12 move centre of pcb to origin
    mounting hole is now at (-0.45, 0.45) (in inches ffs idk)
    [main.brd]
2021-12-12 rotate logo
    [main.brd]
2021-12-25 gerber files using PCBWay CAM
2022-02-26 sensors-datafile mockup running
2022-03-21 extend central cutout
    [main.brd]
2022-03-21 move text to t/b place
    [main.brd]
2022-03-29 Added LED colour indication
2022-04-08 Switched to correct speaker code
    [speaker.py]
2022-04-08 Added actual sensors to sensors
2022-05-14 add STM 1n5819 to schematic
    [main.brd, main.sch]
2022-05-14 connect schottky
    [main.brd, main.sch]
2022-05-14 remove adafruit frame
    [main.sch]
2022-05-14 place diode on pcb
    [main.brd]
2022-05-14 shuffle diode to keep logo plated
    [main.brd]
2022-05-31 added files from board to git
2022-06-20 create souvenir models
    [main_keyring.brd, main_keyring.sch]
2022-06-20 change white noise range to be optimum for speaker
    [speaker.py]
2022-07-01 Did stuff on the board, too tired for proper commit messages - don't do this

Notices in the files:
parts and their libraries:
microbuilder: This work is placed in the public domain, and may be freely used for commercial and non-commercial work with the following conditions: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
